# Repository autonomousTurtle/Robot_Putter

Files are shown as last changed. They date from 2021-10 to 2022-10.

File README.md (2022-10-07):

# Robot_Putter
### [May We Help](https://maywehelp.org/) Putt-Putt Robot



## Controls
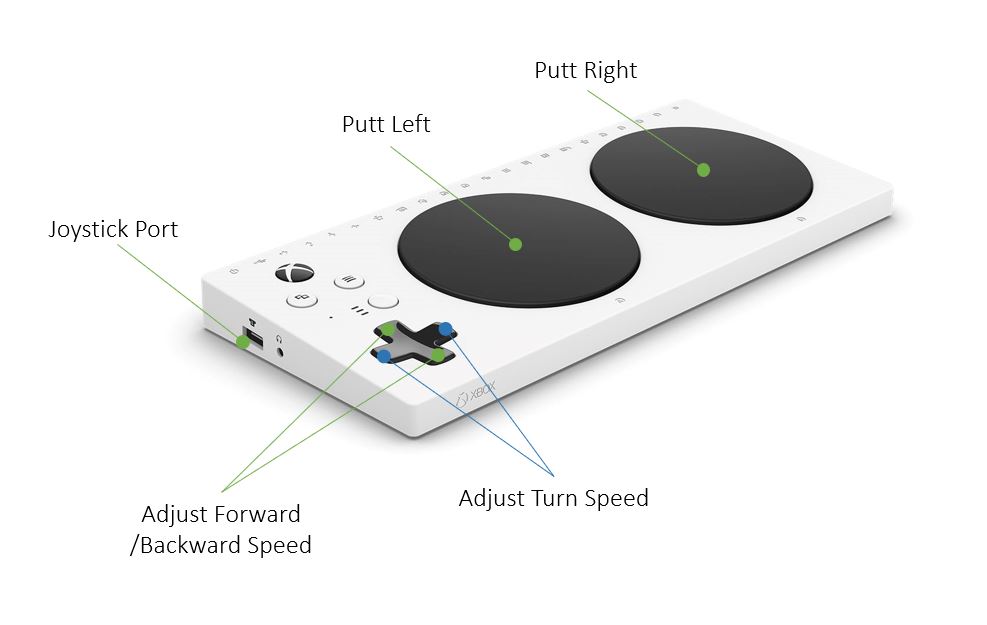
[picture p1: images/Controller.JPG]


## Table Of Contents
1. [BOM](https://github.com/autonomousTurtle/Robot_Putter/blob/main/README.md#bom)
2. [Assembly](https://github.com/autonomousTurtle/Robot_Putter/blob/main/README.md#assembly)
3. [Wiring](https://github.com/autonomousTurtle/Robot_Putter/blob/main/README.md#wiring-images)
4. [Software](https://github.com/autonomousTurtle/Robot_Putter/tree/main/software)

## BOM

### A. Electrical
| Description | Quantity | Ordering Information | Comments |  
| --- | :---: | --- | --- |
|Adafruit Servo Driver Breakout<br>PCA9685|1|[Adafruit](https://www.adafruit.com/product/815)|Adafruit: [Drawings and Tutorials](https://learn.adafruit.com/16-channel-pwm-servo-driver/downloads)|
|Raspberry Pi 4<br>Model B 4GB|1|[CanaKit](https://www.canakit.com/raspberry-pi-4-extreme-kit.html)<br>[Adafruit # 4292](https://www.adafruit.com/product/4292)|CanaKit includes all components necessary to use the pi.<br>Minimum 32GB SD Card|
|Arduino UNO<br>Rev3 ATmega328P|1|[Arduino #A000066](https://store-usa.arduino.cc/products/arduino-uno-rev3)<br>[Sparkfun # DEV-11021](https://www.sparkfun.com/products/11021)|[Elegoo](https://www.elegoo.com/products/elegoo-uno-r3-board) and other brands work fine as well|
|Arduino Shield<br>Through-hole protoboard|1|[Amazon Gikfun](https://www.amazon.com/Gikfun-Prototype-Shield-Arduino-Ek1038x3/dp/B00Q9YB7PI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)|Shields with a 5V and GND rail are the easiest to work with IMO
|Dual Motor Driver<br>L298N|1|[Amazon](https://www.amazon.com/Controller-H-Bridge-Stepper-Control-Mega2560/dp/B07WS89781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)<br>[BC Robotics]https://bc-robotics.com/shop/l298n-motor-driver-board/)|Inludes headers. Drives two DC brushed motors, 1A constant, 3A peak
|12V Battery Pack<br>Dewalt DCB127|[Amazon Dewalt](https://www.amazon.com/DEWALT-DCB127-12V-Lithium-Battery-Pack/dp/B00KYQ1UVS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)<br>[Amazon TenHutt](https://www.amazon.com/dp/B07ZQ9W9RP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)|For use with [12V Dewalt  Charger](https://www.amazon.com/dp/B08FX153FN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)
|Battery Charger<br>Dewalt Charger 12V|1|[Amazon](https://www.amazon.com/dp/B08FX153FN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)
|12V - 6V DC Converter<br>|1|[Amazon](https://www.amazon.com/SMAKN%C2%AE-DC-DC-Converter-Supply-Waterproof/dp/B014ZQ6TFY)|There are many options, most will work. Does not need to be waterproof. Also want to explore this [Digikey R12P06S](https://www.digikey.com/en/products/detail/recom-power/R12P06S/7603362)
|UBEC<br>5V @ 3A DC/DC Buck Converter|1|[Adafruit #1385](https://www.adafruit.com/product/1385)<br>[Amazon](https://www.amazon.com/DEVMO-3amp-6-0-25-2v-Adjustable-Products/dp/B0971H54FQ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)|Used to power the Rasbperry Pi from the 12V battery - must have 5V output, 3A recommended
|Wago Connectors<br>|1|[Digikey 2946-887-952-ND](https://www.digikey.com/en/products/detail/wago-corporation/887-952/15553727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)<br>[Amazon](https://www.amazon.com/Lukche-LEVER-NUTS-Splicing-Connector-Assortment/dp/B095F2Z3DD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)|Other connectors will work (XT60, JST, EC5), Wago simply make it easy to prototype. 

### B. Electro-Mechanical 
| Description | Quantity | Ordering Information | Comments |  
| --- | :---: | --- | --- |
|Putter Servo Motor<br>30KG 270 Degree DS3230|1|[Amazon](https://www.amazon.com/DS3230-30KG-Degree-Digital-Servo/dp/B07VN6F179)<br> [Amazon LJWRC](https://www.amazon.com/LJWRC-DS3230MG-Waterproof-Digital-Degree/dp/B088KJGM4C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)|6.8 V, Full metal gear, waterproof, includes 25T metal servo hub
|Tank Tread Base<br>SZDoit T300|1|[Amazon SZDoit](https://www.amazon.com/dp/B08HRTZNHW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)|Includes qty 2 9V DC motors with encoders
|12V High Torque Motors<br>Geartesian 550RPM|2|[Amazon](https://www.amazon.com/Greartisan-Electric-Reduction-Centric-Diameter/dp/B072R5G5GR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)|
|Adaptive Controller<br>XBox|1|[Best Buy](https://www.bestbuy.com/site/microsoft-xbox-adaptive-controller-white/6455394.p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)|[Any switch with a 3.5mm jack](https://www.ablenetinc.com/switches/all-switches/) can be used with this controller. 
|Warfighter Engaged<br>Joystick FPS|1|[Warfighter](https://warfighterengaged.org/shop/joystix-l-aenef)

### C. Mechanical

| Description | Quantity | Ordering Information | Comments |  
| --- | :---: | --- | --- |
|Printer Filament<br>PLA|1|[MatterHackers M-EED-KTKU](https://www.matterhackers.com/store/l/175mm-pla-filament-white-1-kg/sk/MEEDKTKU)| Color does not matter. Diameter for most filament printers should be 1.75mm |
|Ball Bearing<br>Shielded|1|[Mcmaster ]([https://www.matterhackers.com/store/l/175mm-pla-filament-white-1-kg/sk/MEEDKTKU](https://www.mcmaster.com/5972K293/))| For 30mm shaft diameter |

### D. 3D Prints
All of the custom parts are 3D Printed on a filamnet printer with PLA. 

| Description | Quantity | Ordering Information | Comments |  
| --- | :---: | --- | --- |
|Putter Servo Mount|1|[Putter_Servo_holder_A.STL](https://github.com/autonomousTurtle/Robot_Putter/blob/main/3D%20Prints/Putter_Servo_holder_A.STL) <br> [Putter_Servo_holder_B.STL](https://github.com/autonomousTurtle/Robot_Putter/blob/main/3D%20Prints/Putter_Servo_holder_B.STL) | Holds the 30kg-cm servo, left and right parts |
|Ball Bearing Inner Housing|1|[BallBearingAttachToRobot_Big_1.STL](https://github.com/autonomousTurtle/Robot_Putter/blob/main/3D%20Prints/BallBearingAttachToRobot_Big_1.STL)| Mounts to Cover Front part |
|Ball Bearing Outer Housing|1|[BallBearingAttachToRobot_little_1.STL](https://github.com/autonomousTurtle/Robot_Putter/blob/main/3D%20Prints/BallBearingAttachToRobot_little_1.STL)| Holds ball bearing in place wtih the inner housing |
|Servo Horn Attachment|1|[GolfClubAttach_rev2_bottom_1.STL](https://github.com/autonomousTurtle/Robot_Putter/blob/main/3D%20Prints/GolfClubAttach_rev2_bottom_1.STL)| Attaches the servo horn and fits inside of the ball bearing |
|Putter Shaft Holder|1|[GolfClubAttach_rev2_top_1.STL](https://github.com/autonomousTurtle/Robot_Putter/blob/main/3D%20Prints/GolfClubAttach_rev2_top_1.STL)| Attaaches to the putter shaft on one end and to the Servo Horn Attachment on the other end |
|Putter Head|1|[PutterHead.STL](https://github.com/autonomousTurtle/Robot_Putter/blob/main/3D%20Prints/PutterHead.STL)| Feel free to use whatever putter head you want, but 3D printing makes the robot lighter |
|Motor Driver Breakout Board Mount|1|[Motor_Driver_Board_Holder_rev1.STL](https://github.com/autonomousTurtle/Robot_Putter/blob/main/3D%20Prints/Motor_Driver_Board_Holder_rev1.STL)| Mounts the L298N breakout board to the bottom plate of the robot base |
|Arduino Uno Mount|1|[Arduino_mount.STL](https://github.com/autonomousTurtle/Robot_Putter/blob/main/3D%20Prints/Arduino_mount.STL)| Used for attaching the Uno to the top of the raspberry pi cana kit case |
|Servo Driver Board Mount|1|[Servo_Driver_Mount.STL](https://github.com/autonomousTurtle/Robot_Putter/blob/main/3D%20Prints/Servo_Driver_Mount.STL)| Attach the servo driver to the base plate |
|Cover Front|1|[cover_front_0.STL](https://github.com/autonomousTurtle/Robot_Putter/blob/main/3D%20Prints/cover_front_0.STL)| Covers the front of the robot internals |
|Cover Rear|1|[cover_back_0.STL](https://github.com/autonomousTurtle/Robot_Putter/blob/main/3D%20Prints/cover_back_0.STL)| Covers the rear of the robot internals |
|Cover Top|1|[cover_top_cover_0.STL](https://github.com/autonomousTurtle/Robot_Putter/blob/main/3D%20Prints/cover_top_cover_0.STL) | I used clear Lexan for this, but you can also 3D print it |

### Assembly

#### Parts Laid Out
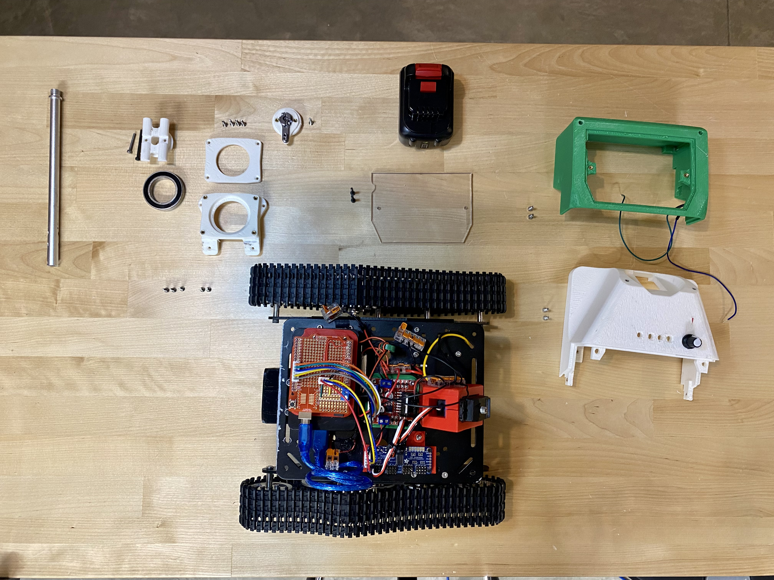
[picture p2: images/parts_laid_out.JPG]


#### Bottom Side
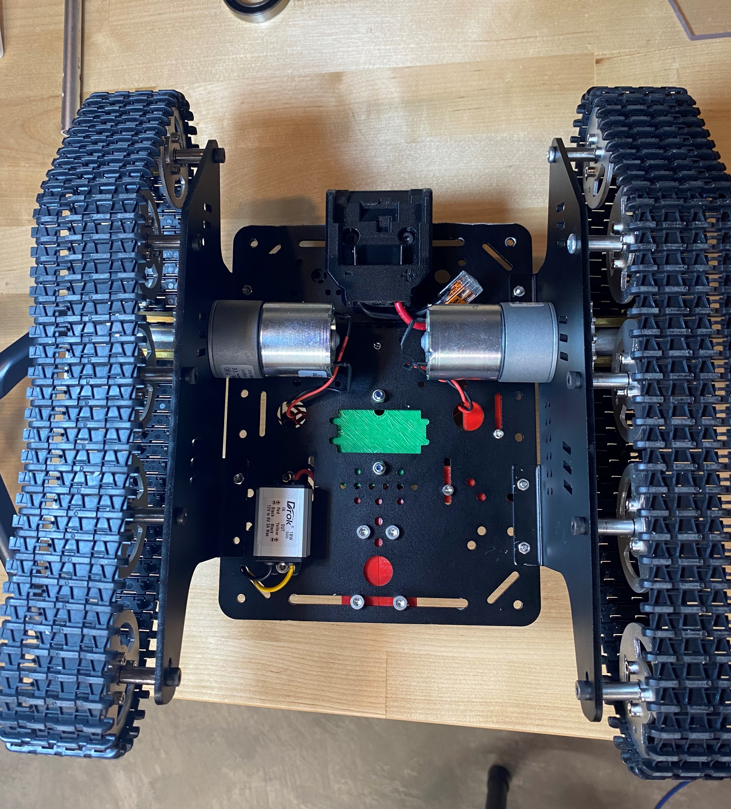
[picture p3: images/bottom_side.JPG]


#### Top Without Cover
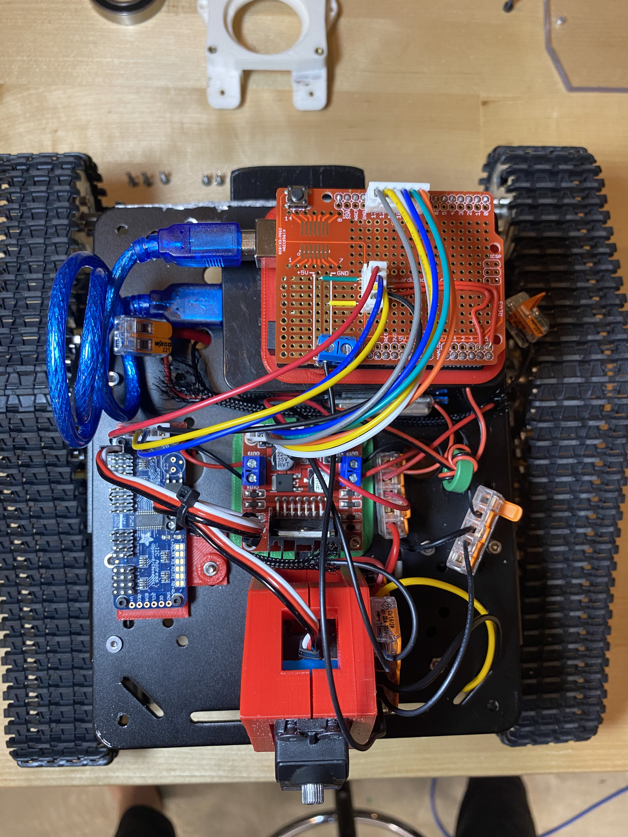
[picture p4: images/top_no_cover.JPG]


### Wiring Images
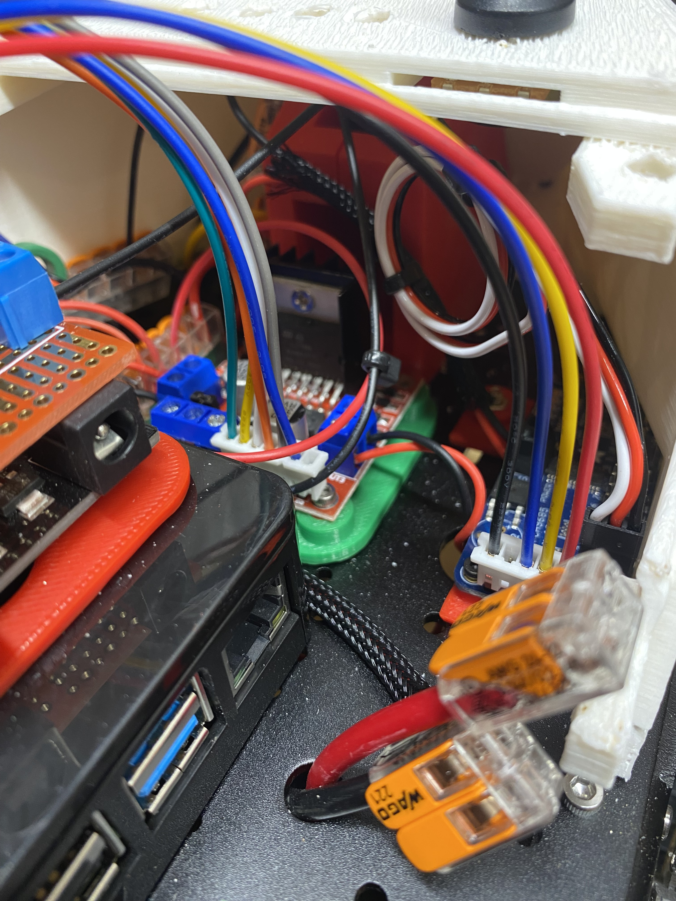
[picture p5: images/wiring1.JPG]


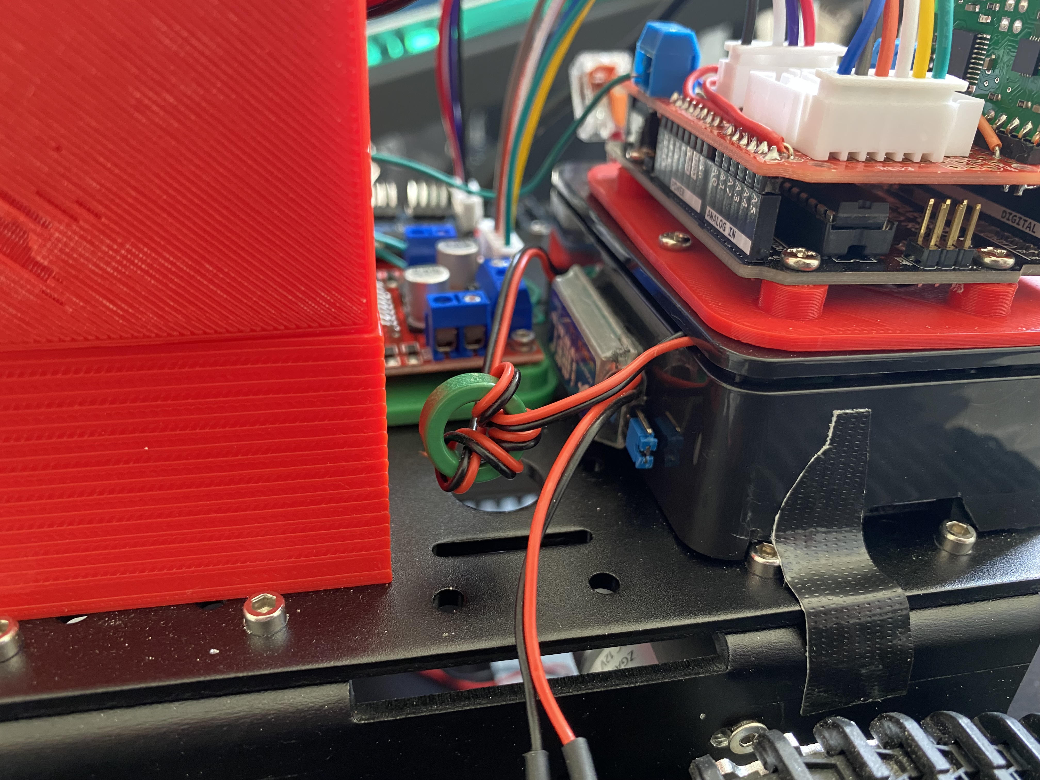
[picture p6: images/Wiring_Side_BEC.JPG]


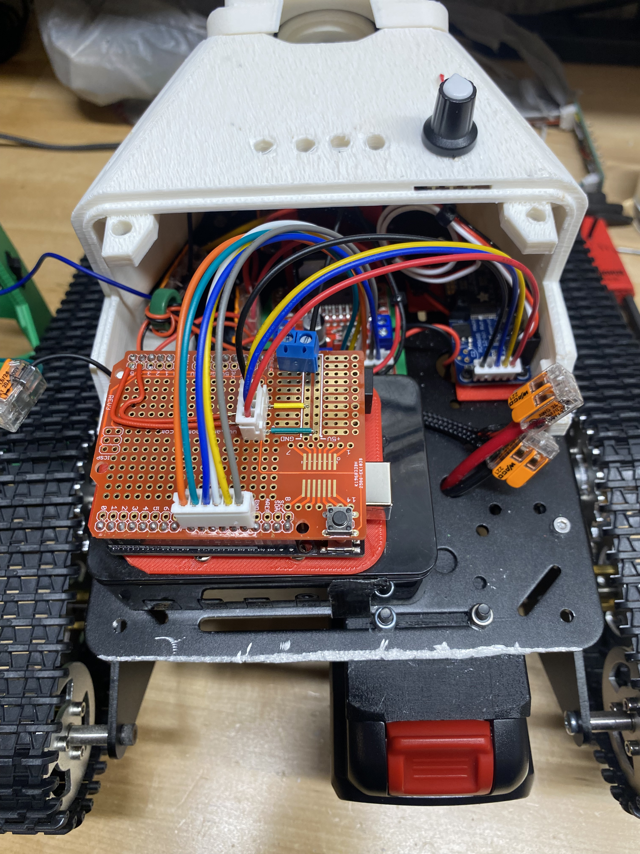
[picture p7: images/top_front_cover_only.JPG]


### Software Architecture:

* Arduino:  software/drive_and_putt/drive_and_putt.ino
* Raspberry Pi: software/deployed/drive_robot.py

See the [software readme for more details](https://github.com/autonomousTurtle/Robot_Putter/tree/main/software)

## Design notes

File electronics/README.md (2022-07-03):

# ROBOT PUTTER ELECTRONICS

### Detailed Wiring
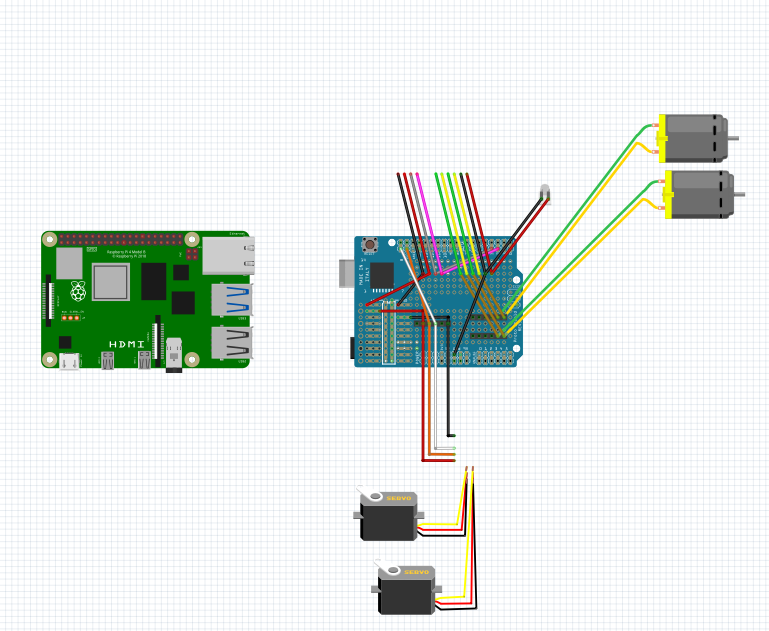
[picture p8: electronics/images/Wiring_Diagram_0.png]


### 1. Electrical Components
| Description | Quantity | Ordering Information | Comments |  
| --- | :---: | --- | --- |
|Adafruit Servo Driver Breakout<br>PCA9685|1|[Adafruit](https://www.adafruit.com/product/815)|Adafruit: [Drawings and Tutorials](https://learn.adafruit.com/16-channel-pwm-servo-driver/downloads)|
|Raspberry Pi 4<br>Model B 4GB|1|[CanaKit](https://www.canakit.com/raspberry-pi-4-extreme-kit.html)<br>[Adafruit # 4292](https://www.adafruit.com/product/4292)|CanaKit includes all components necessary to use the pi.<br>Minimum 32GB SD Card|
|Arduino UNO<br>Rev3 ATmega328P|1|[Arduino #A000066](https://store-usa.arduino.cc/products/arduino-uno-rev3)<br>[Sparkfun # DEV-11021](https://www.sparkfun.com/products/11021)|[Elegoo](https://www.elegoo.com/products/elegoo-uno-r3-board) and other brands work fine as well|
|Arduino Shield<br>Through-hole protoboard|1|[Amazon Gikfun](https://www.amazon.com/Gikfun-Prototype-Shield-Arduino-Ek1038x3/dp/B00Q9YB7PI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)|Shields with a 5V and GND rail are the easiest to work with IMO
|Dual Motor Driver<br>Pololu Qik 2s9v1|1|[Pololu #1110](https://www.pololu.com/product/1110)<br>[DigiKey # 2183-1110-ND](https://www.digikey.com/en/products/detail/pololu-corporation/1110/10450402)|Inludes headers. Drives two DC brushed motors, 1A constant, 3A peak
|12V Battery Pack<br>Tenergy 2000mAh NiMH|2|[Amazon](https://www.amazon.com/Tenergy-Capacity-Rechargeable-Replacement-Equipments/dp/B077Y9HNTF?th=1)<br>[Tenergy Power #11606](https://power.tenergy.com/tenergy-nimh-12v-2000mah-battery-pack-w-bare-leads/)|Requires [T-Plug headers](https://www.progressiverc.com/products/t-plug-connectors) <br>For use with [6V-12V Tenergy Smart Charger](https://power.tenergy.com/tenergy-smart-universal-charger-for-nimh-nicd-battery-packs-6v-12v-ul/)
|Battery Charger<br>Tenergy NiMH Charger 6-12V|1|[Tenergy Power #01025](https://power.tenergy.com/tenergy-smart-universal-charger-for-nimh-nicd-battery-packs-6v-12v-ul/)|Can also use [Tenergy NiHM 7.2-12V Charger](https://power.tenergy.com/tenergy-smart-universal-charger-for-nimh-nicd-battery-packs-7-2v-12v-ul/)
|AI 3D Camera<br>Luxonis OAK-D|1|[Luxonis OAK-D](https://shop.luxonis.com/products/oak-d)<br>[DigiKey #SEN-17770](https://www.digikey.in/en/products/detail/sparkfun-electronics/SEN-17770/13901888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)|Requires high throughput USBC cable, inlcuded with camera
|12V - 6V DC Converter<br>|1|[Amazon](https://www.amazon.com/SMAKN%C2%AE-DC-DC-Converter-Supply-Waterproof/dp/B014ZQ6TFY)|There are many options, most will work. Does not need to be waterproof. Also want to explore this [Digikey R12P06S](https://www.digikey.com/en/products/detail/recom-power/R12P06S/7603362)
|UBEC<br>5V @ 3A DC/DC Buck Converter|1|[Adafruit #1385](https://www.adafruit.com/product/1385)<br>[Amazon](https://www.amazon.com/DEVMO-3amp-6-0-25-2v-Adjustable-Products/dp/B0971H54FQ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)|Used to power the Rasbperry Pi from the 12V battery - must have 5V output, 3A recommended
|T-Plug Connectors<br>|1|[ProgressiveRC #AC-TC](https://www.progressiverc.com/products/t-plug-connectors)<br>[Amazon](https://www.amazon.com/Hobbypark-T-Plug-Connectors-Battery-Electric/dp/B01C8NWJ78)|Other battery connectors will work (XT60, JST, EC5) just make sure it is secure. 
|Wire Heat Shirnk Wrap<br>|1|[Amazon](https://www.amazon.com/650pcs-Shrink-Tubing-innhom-Approved/dp/B07WWWPR2X)<br>|A kit with a variety of sizes helps to have what is needed for different wire gauges

### 2. Electro-Mechanical 
| Description | Quantity | Ordering Information | Comments |  
| --- | :---: | --- | --- |
|Putter Servo Motor<br>30KG 270 Degree DS3230|1|[Amazon](https://www.amazon.com/DS3230-30KG-Degree-Digital-Servo/dp/B07VN6F179)<br> [Amazon LJWRC](https://www.amazon.com/LJWRC-DS3230MG-Waterproof-Digital-Degree/dp/B088KJGM4C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)|6.8 V, Full metal gear, waterproof, includes 25T metal servo hub
|Camera Servo Motor<br>20KG 270 Degree DS3218MG|1|[Amazon ANNIMOS](https://www.amazon.com/ANNIMOS-Digital-Waterproof-DS3218MG-Control/dp/B076CNKQX4)<br>[Amazon ZOSKAY](https://www.amazon.com/ZOSKAY-DS3218-Digital-Waterproof-Control/dp/B01MU7TQV8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)|6.8 V, Full metal gear, waterproof, includes 25T metal servo hub
|Tank Tread Base<br>SZDoit T300|1|[Amazon SZDoit](https://www.amazon.com/dp/B08HRTZNHW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)|Includes qty 2 9V DC motors with encoders
|Adaptive Controller<br>Nintendo HORI Flex|1|[HORI #NSW-280U](https://stores.horiusa.com/flex-controller-for-nintendo-switch/?showHidden=true)|[Any switch with a 3.5mm jack](https://www.ablenetinc.com/switches/all-switches/) can be used with this controller.

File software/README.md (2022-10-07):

# SOFTWARE 

## Overview: 

This robot uses [subsumption control architecure](https://en.wikipedia.org/wiki/Subsumption_architecture) to manage both a Raspberry Pi and an Arduino microcontroller. The Arduino is responsible for the low level management: motor control, servo control, LED control. The Raspberry Pi is responsible for the higer level control: talking to the XBox controller, ensure the robot si driving straight, when to move the putter vs when to move the motors, speed ramping and more. 

In this architecture, the raspberry pi is sending strings of commands to the Arduino. The Arduino looks at the commands and executes the necessary code to make the desired actions happen. When there are no actions called for from the Pi, they communicate back and forth at 2hz with a heartbeat. If the Pi or Arduino fail to send or recieve a heartbeat signal, they will stop all motion and shut down their processes. This is an important safety mechanism to prevent run-away robots! 

## Code: 
**Python Script run on Raspberry Pi:** [drive_robot.py](https://github.com/autonomousTurtle/Robot_Putter/blob/main/software/deployed/drive_robot.py)

_this code will start automatically with an auto-run script, but to run manually through ssh, navigate to the root folder and type:_

`$ python3 drive_robot.py`

**Arduino Script:** [drive_and_putt.ino](https://github.com/autonomousTurtle/Robot_Putter/blob/main/software/drive_and_putt/drive_and_putt.ino)

## Rapsberry Pi Connections:

### LAN
Raspberry Pi eth0 IP: 192.168.0.1 (ethernet port on the Pi)
Raspberry Pi LAN IP: 192.168.7.21

### WAN and SSH
username: pi@192.168.7.129
password: raspberry

## Configuring the Raspberry Pi:

### Serial
You need to configure serial on the Pi to be able to talk to Aruduino board. You do this by giving the user dialout permissions:

`usermod -a -G dialout $USER`

### Auto Run Python Script 
We need to automatically run the drive_robot.py script on boot of the rpi. [Link here is hlepful to get it set up](https://www.codementor.io/@ufukafak/how-to-run-a-python-script-in-linux-with-systemd-1nh2x3hi0e_)

## Pi Libraries:

### Read Controller Inputs
[PiBorg Gamepad Library](https://www.piborg.org/blog/gamepad-library): [Github Link](https://github.com/piborg/Gamepad)

This library is great becuases it has built in asynchronous updates in a background thread. 

```
import Gamepad
gamepad = Gamepad.PS4()

# Start the background updating
gamepad.startBackgroundUpdates()

# Your code here :)

# Stop the background thread
gamepad.disconnect()
```

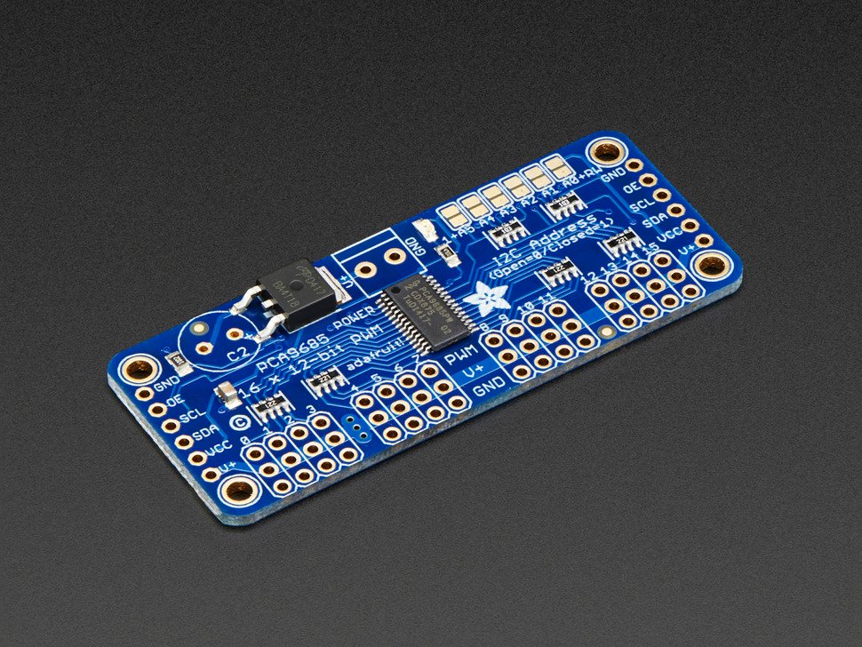
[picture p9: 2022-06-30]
electronics/images/adafruit_servo_breakout.jpg

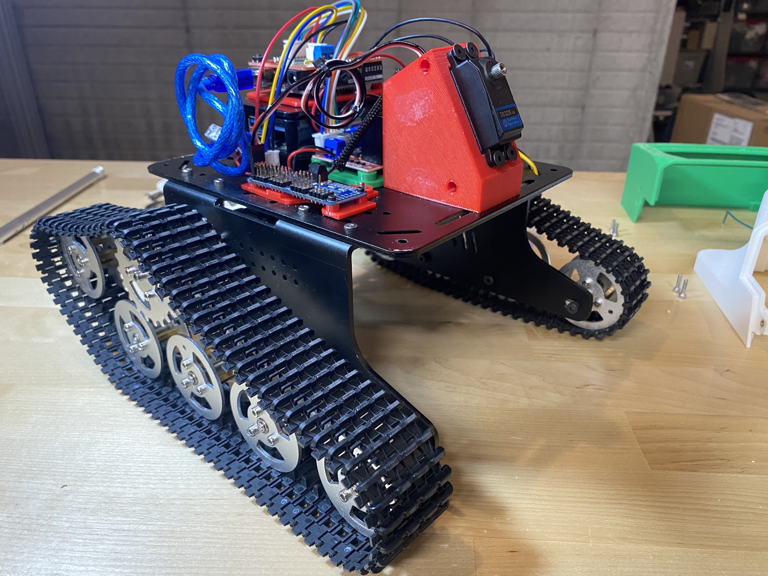
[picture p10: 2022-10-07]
images/iso_no_cover.JPG

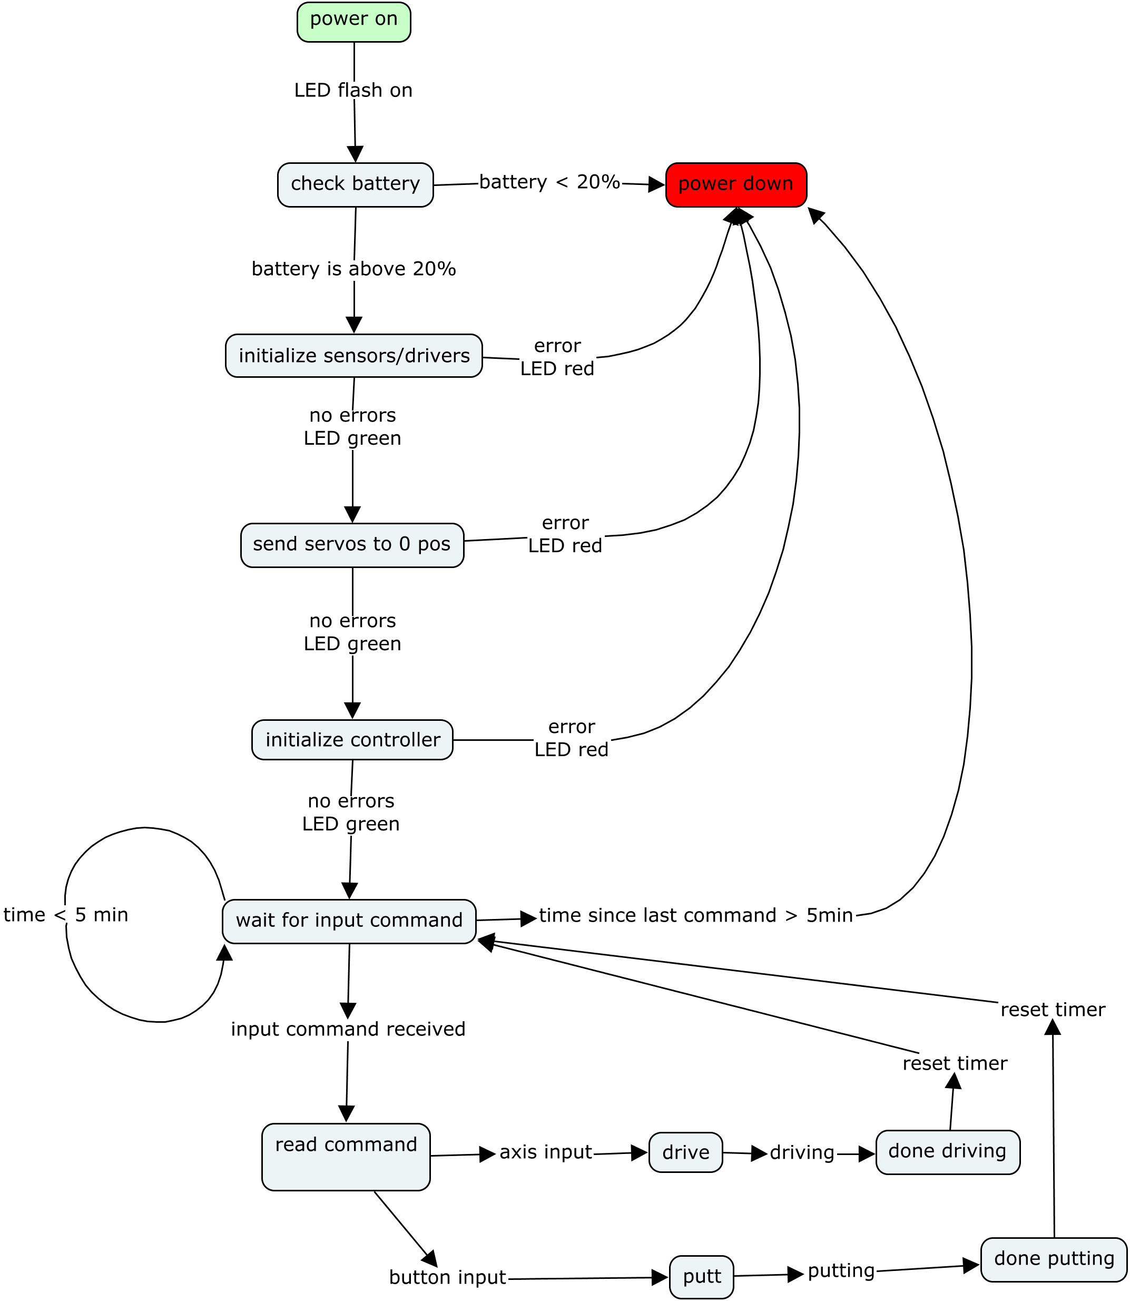
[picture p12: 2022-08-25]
software/Putt Robot State Machine.png

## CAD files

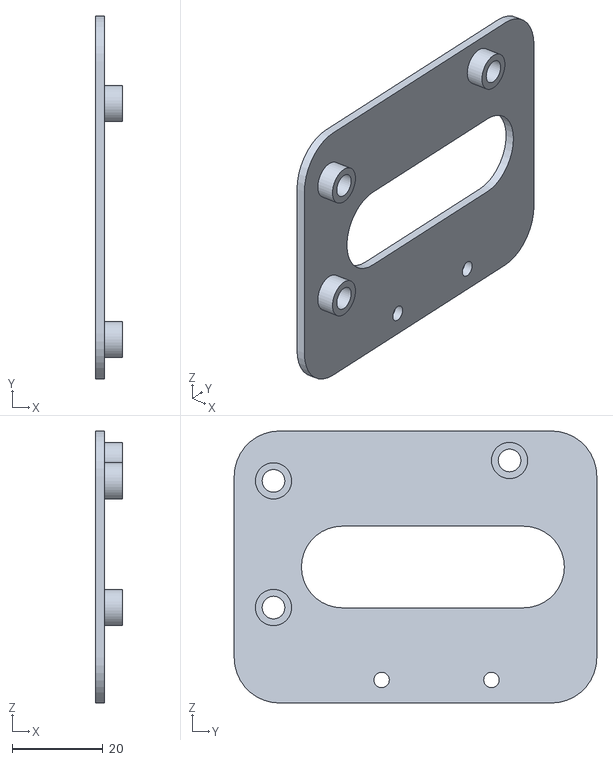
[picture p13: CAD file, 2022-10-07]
3D Prints/Arduino_mount.STL
6.00 x 80.0 x 60.0

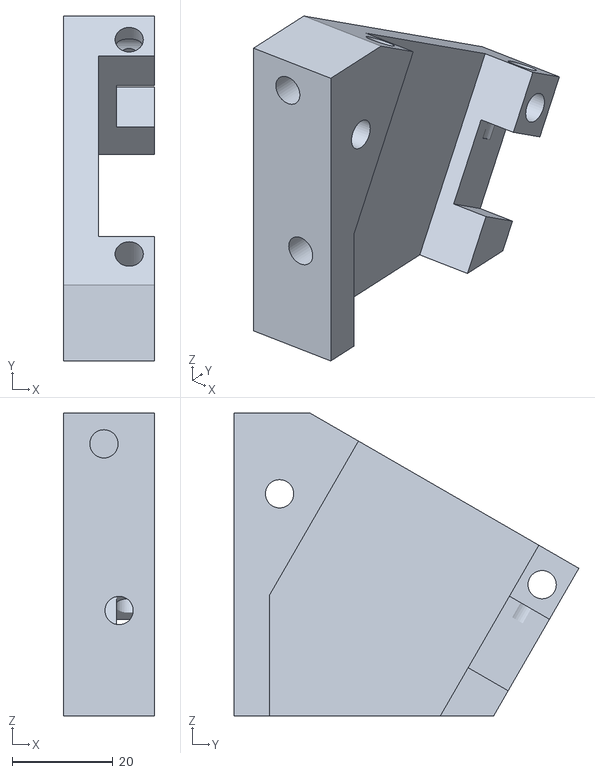
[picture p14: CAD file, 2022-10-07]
3D Prints/Putter_Servo_holder_A.STL
18.0 x 68.3 x 60.0

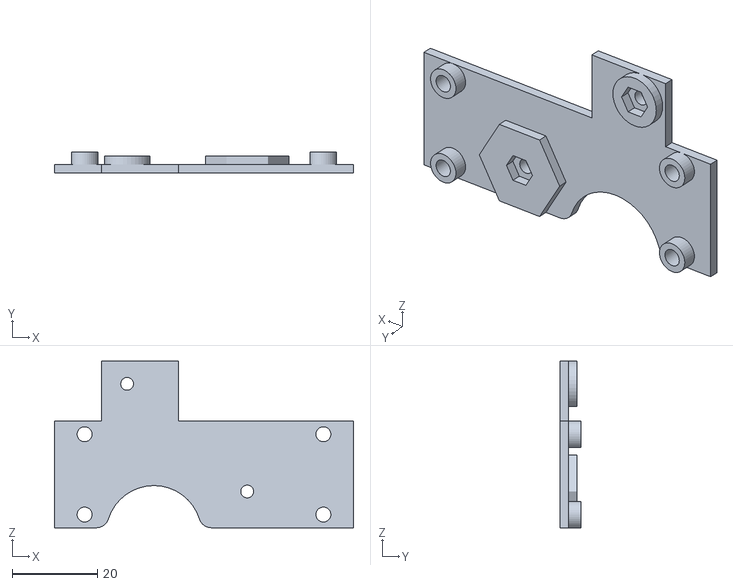
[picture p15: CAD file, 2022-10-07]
3D Prints/Servo_Driver_Mount.STL
70.0 x 5.00 x 39.0

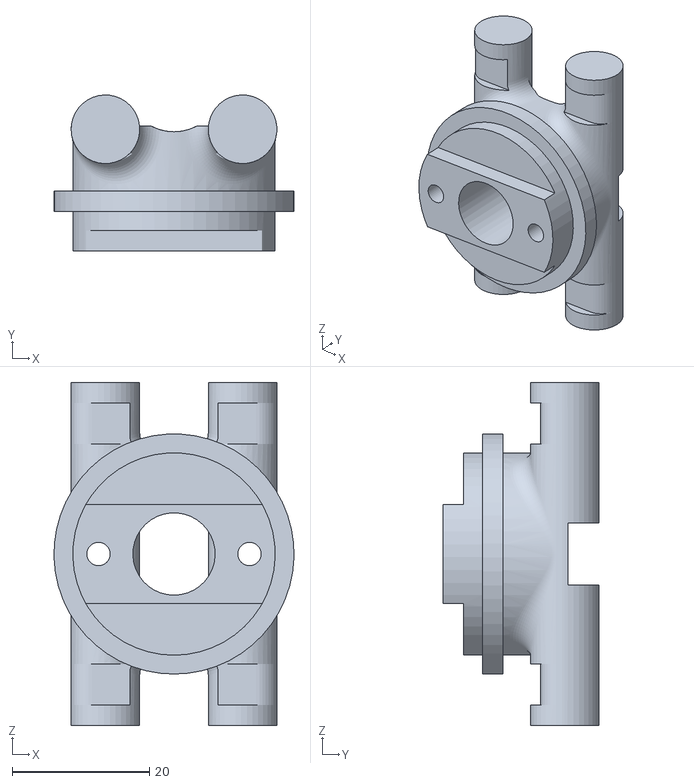
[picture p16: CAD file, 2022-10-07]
3D Prints/GolfClubAttach_rev2_top_1.STL
35.0 x 22.7 x 50.0

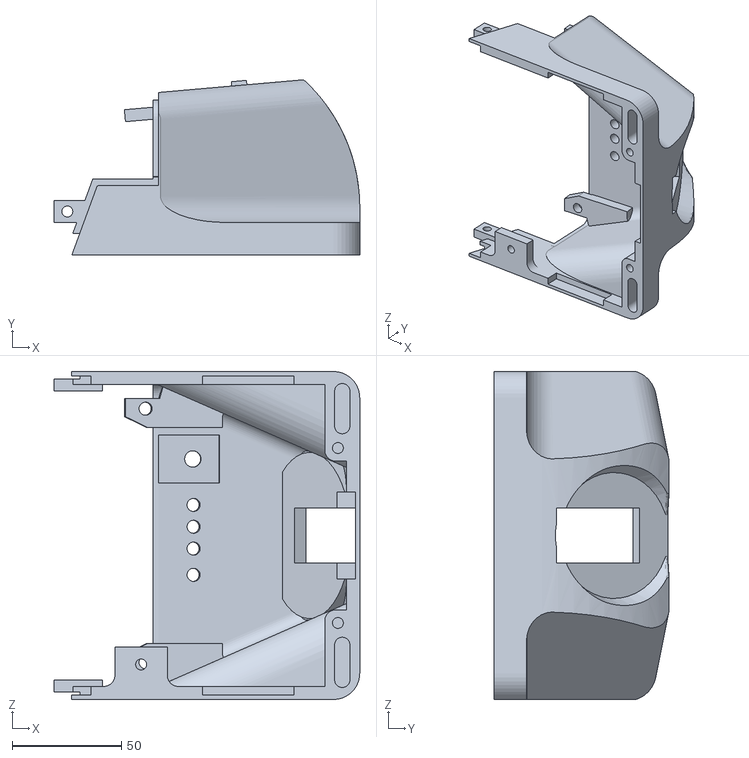
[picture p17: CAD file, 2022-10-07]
3D Prints/cover_front_0.STL
139.7 x 80.3 x 150.0

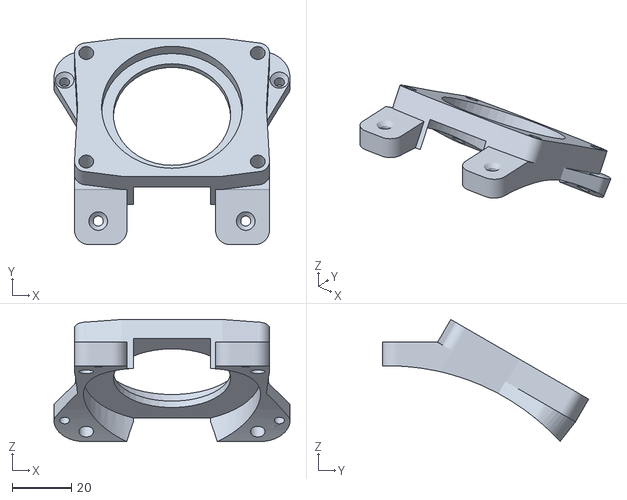
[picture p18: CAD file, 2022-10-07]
3D Prints/BallBearingAttachToRobot_Big_1.STL
80.0 x 70.0 x 41.4

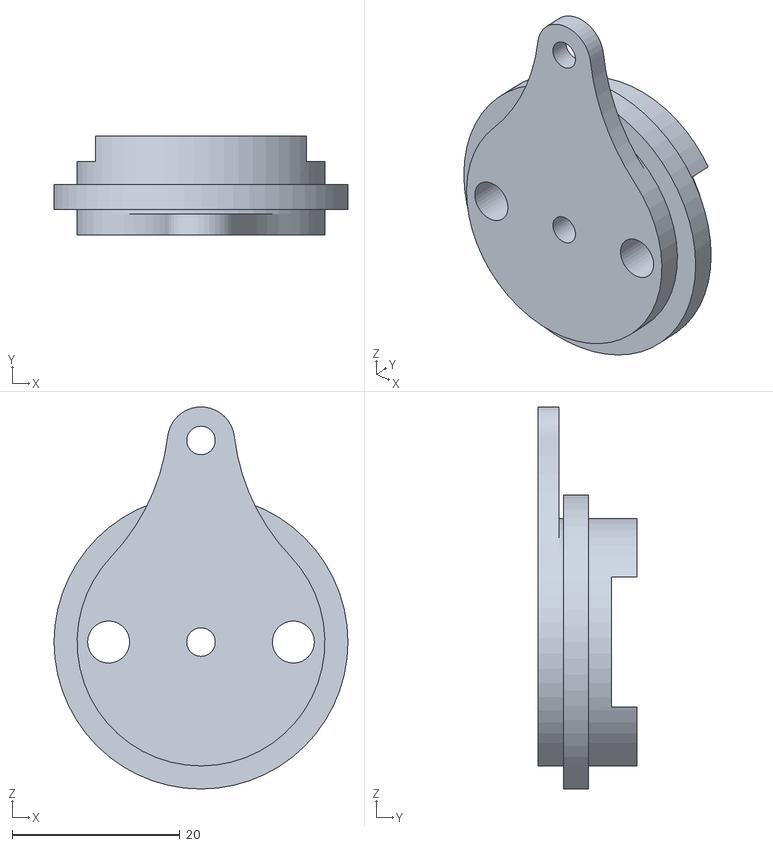
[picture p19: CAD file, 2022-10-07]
3D Prints/GolfClubAttach_rev2_bottom_1.STL
35.0 x 11.8 x 45.5

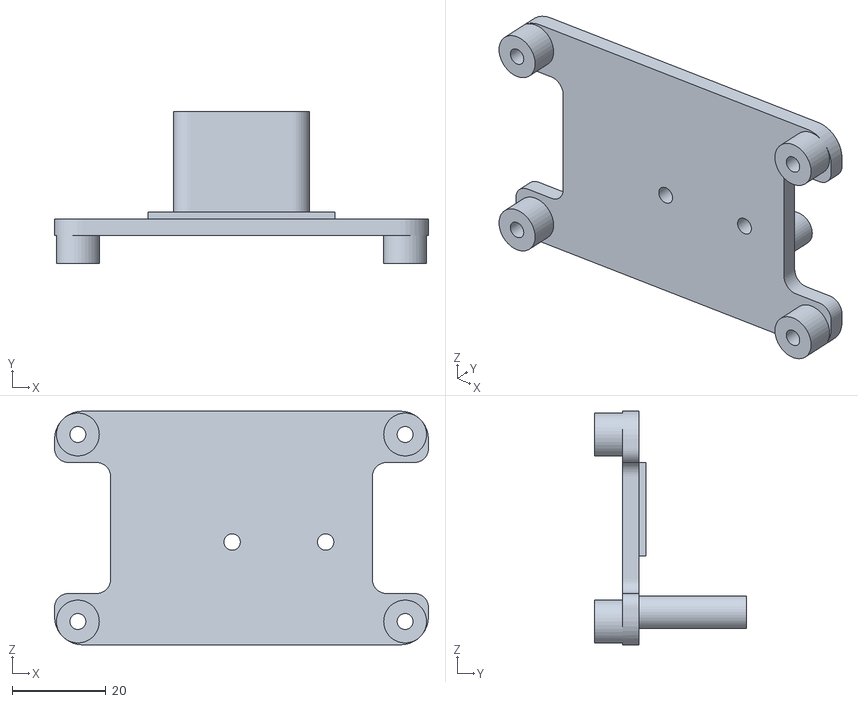
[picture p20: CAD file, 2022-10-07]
3D Prints/Motor_Driver_Board_Holder_rev1.STL
80.0 x 32.5 x 50.0

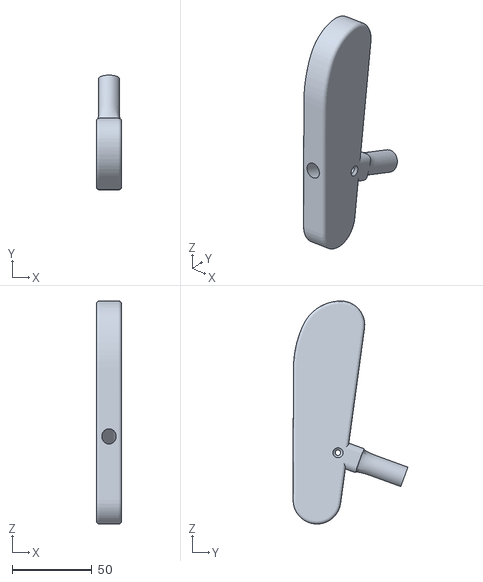
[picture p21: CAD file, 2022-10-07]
3D Prints/PutterHead.STL
16.0 x 72.1 x 140.0

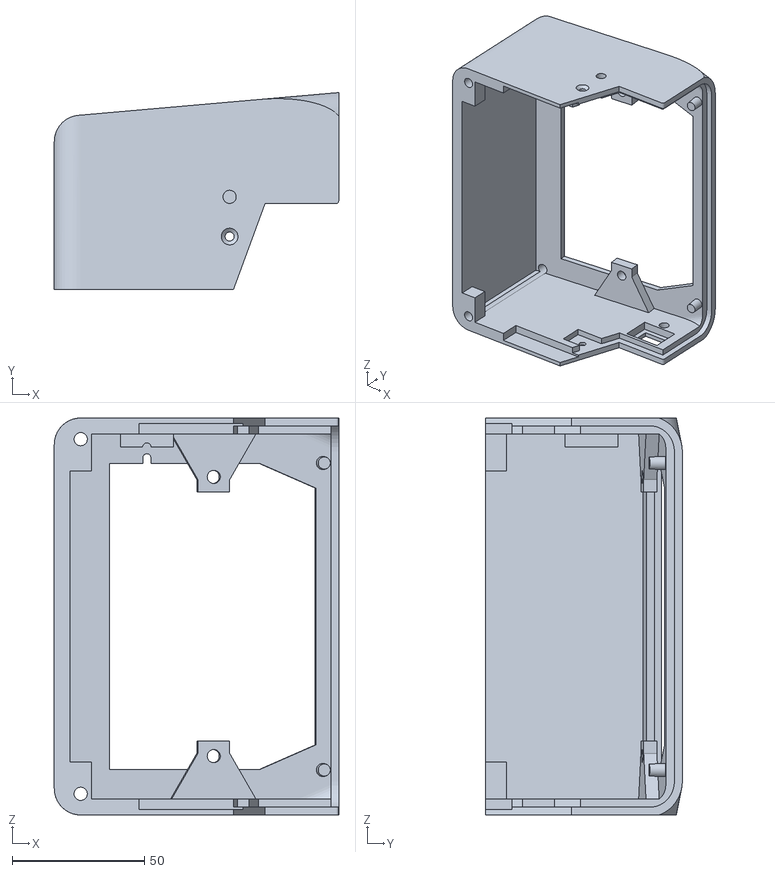
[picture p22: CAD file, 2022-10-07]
3D Prints/cover_back_0.STL
107.5 x 74.4 x 150.0

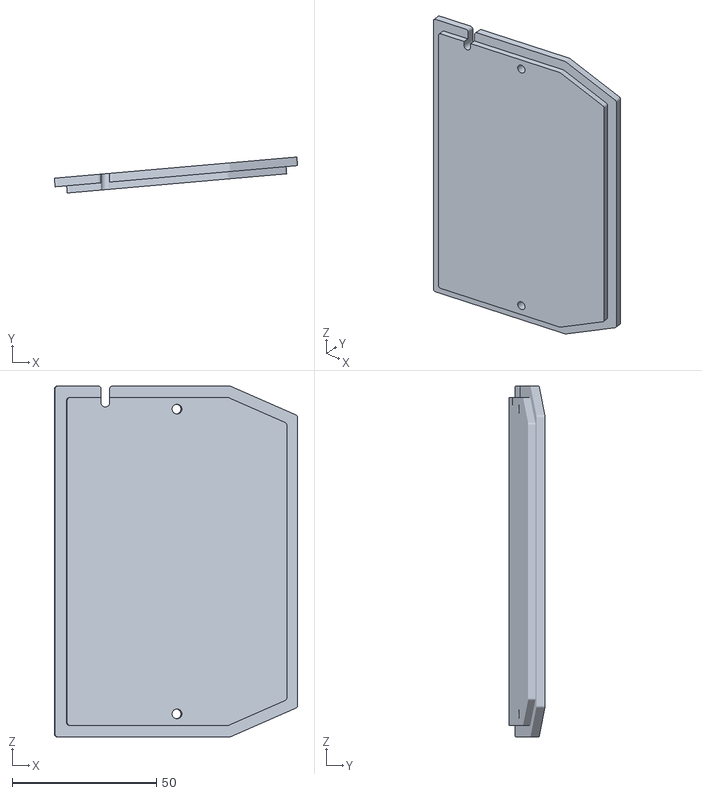
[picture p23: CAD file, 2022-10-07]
3D Prints/cover_top_cover_0.STL
84.2 x 12.5 x 121.5

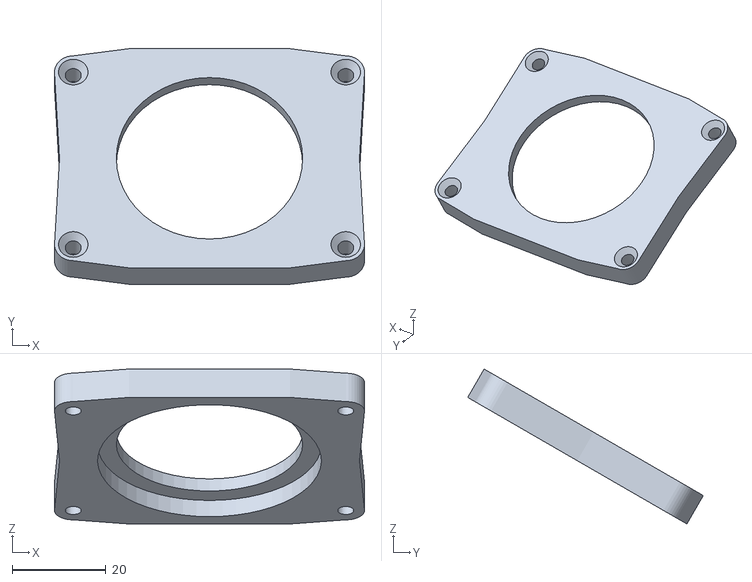
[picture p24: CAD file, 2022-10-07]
3D Prints/BallBearingAttachToRobot_little_1.STL
66.1 x 50.3 x 33.1

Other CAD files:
3D Prints/Putter_Servo_holder_B.STL

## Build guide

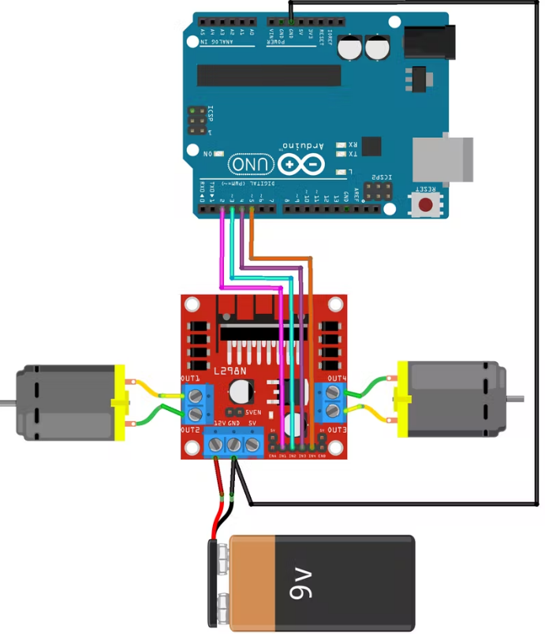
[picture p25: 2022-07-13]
software/images/L298N Wiring.png

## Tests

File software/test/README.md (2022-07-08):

# Test Software

For all tests, run the python script on the Raspberry Pi and .ino script on the Arduino
## Communication Test

### Python Script: 
Takes in keyboard w,a,s,d inputs and sends fake commands to the arduino. It also sends a heartbeat meassage twice a second. 

### Arduino Script: 

## Motor Test
### Python Script: 

### Arduino Script:

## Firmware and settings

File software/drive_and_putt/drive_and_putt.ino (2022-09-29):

/***************************************************

  Online Libraries:
  Timer.h - JChristhensen's Timer Library https://github.com/JChristensen/Timer
  Event.h - Arcturial arduino event https://github.com/arcturial/arduino-event
  Link to the Adafruit PWM Servo Driver  http://www.adafruit.com/products/815

  Link to Raspberry Pi to Arduino Serial Comm:
  https://www.aranacorp.com/en/serial-communication-between-raspberry-pi-and-arduino/


 ****************************************************/

#include <Adafruit_PWMServoDriver.h>
#include <Wire.h>
#include <Timer.h>
#include <Event.h>


// ---------- L298N Motor Driver ---------
#define enA 9
#define in1 12
#define in2 11
#define in3 8
#define in4 13
#define enB 10


// ---------- LED Pins ---------
#define LED1 3  // status LED, green is online and HB is good
#define LED2 2
#define LED3 4
#define LED4 5


// ---------- SERVO DRIVER -----------
Adafruit_PWMServoDriver pwm = Adafruit_PWMServoDriver(); // called this way, it uses the default address 0x40

#define SERVOMIN  150 // This is the 'minimum' pulse length count (out of 4096)
#define SERVOMAX  600 // This is the 'maximum' pulse length count (out of 4096)
#define SERVO_FREQ 50 // Analog servos run at ~50 Hz updates

// Servo home positions (in microsecond length)
const int servo0_home = 300;
const int servo1_home = 280;


// ---------- RASBPERRY PI COMMS ----------
int timerEvent;
int hti; //heartbeat timeout interfal
boolean hbb; //heartbeat fail indication
Timer timer;
const byte inDataLen = 28;
char inData[inDataLen]; // buffer input commands
char messageFromPC[inDataLen] = {0};
double HBBtime = 0;
double LMotorInput;
double RMotorInput;

boolean newData = false; // detect new data into the arduino from the pi

boolean between(int in, int lower, int upper) {
  boolean result = false;
  if ((in <= upper) && (in >= lower)) {
    result = true;
  }
  return result;
}


void clearHBB() {
  hbb = false;
  timerEvent = timer.after(hti, clearHBB);
  // stop all of the motors
  analogWrite(enA, 0); // Send PWM signal to L298N Enable pin
  analogWrite(enB, 0); // Send PWM signal to L298N Enable pin
  digitalWrite(LED1, LOW);
}


void ALLSTOP() {
  analogWrite(enA, 0); // Send PWM signal to L298N Enable pin
  analogWrite(enB, 0); // Send PWM signal to L298N Enable pin
  Serial.write("All Stop\n");
}


void setup() {
  // Start serial communication with the PC
  Serial.begin(115200);
  hti = 1000;
  timerEvent = timer.after(hti, clearHBB);
  
  // ---------- L298N Pin Settings ---------
  pinMode(enA, OUTPUT);
  pinMode(in1, OUTPUT);
  pinMode(in2, OUTPUT);
  pinMode(enB, OUTPUT);
  pinMode(in3, OUTPUT);
  pinMode(in4, OUTPUT);

  pinMode(LED1, OUTPUT);
  pinMode(LED2, OUTPUT);
  pinMode(LED3, OUTPUT);
  pinMode(LED4, OUTPUT);
  

  // Set initial rotation direction
  digitalWrite(in1, LOW);
  digitalWrite(in2, HIGH);

  digitalWrite(LED1, LOW);
  digitalWrite(LED2, LOW);
  digitalWrite(LED3, LOW);
  digitalWrite(LED4, LOW);

  // servo driver
  pwm.begin();
  pwm.setOscillatorFrequency(27000000);
  pwm.setPWMFreq(SERVO_FREQ);  // Analog servos run at ~50 Hz updates


  delay(100); 

  // set servos to 0 position
  pwm.setPWM(0, 0, servo0_home); // putter servo
  pwm.setPWM(1, 0, servo1_home); // camera servo

  Serial.println("ready >");

  delay(500);

}

void loop() {
  char EOL = '>';
  static byte ndx = 0;

  timer.update();

  if (Serial.available() > 0) {
    char inChar = Serial.read();

    if (inChar != EOL) {
      inData
      [ndx] = inChar;
      ndx++;
      if (ndx >= inDataLen) {
        ndx =  inDataLen - 1;
      }
    }
    else if (inChar == EOL) {
      inData[ndx] = '\0'; // terminate the string
      ndx = 0;
      newData = true;
    }
  }

  if (newData == true) {

    // parse the data commas are the seperator

    // split the data into its parts
    char * strtokIndx; //
    strtokIndx = strtok(inData, ","); // get the first part, the string (HBB, DRV, STP..)
    strcpy(messageFromPC, strtokIndx); // copy the string to the messageFromPC char


    if (messageFromPC[0] == 'S') {
      // stop!
      Serial.print("STOP CMD\n");
      ALLSTOP();
      digitalWrite(LED1, LOW); //status LED on 
    }

    // heartbeat - check this first
    if (messageFromPC[0] == 'H') {
      digitalWrite(LED1, HIGH); //status LED on 
      // parse the time data
      strtokIndx = strtok(NULL, ","); // continues where we left off in the message
      //strcpy(HBBtime, strtokIndx);
      //Serial.print(strtokIndx);
      HBBtime = atof(strtokIndx);

      // just put it right back out the serial port
      Serial.print("HBB ");
      Serial.print(HBBtime);
      Serial.println(">");
      hbb = true;
      timer.stop(timerEvent); //candel the last timer
      // set a timer that goes off in 2 seconds
      timerEvent = timer.after(hti, clearHBB);
      
    }

    if (messageFromPC[0] == 'D') {
      hbb = true;
      digitalWrite(LED1, HIGH); //status LED on 
      timer.stop(timerEvent);
      timerEvent = timer.after(hti, clearHBB);
      // parse data

      strtokIndx = strtok(NULL, ","); // continues where we left off in the message
      RMotorInput = atof(strtokIndx);
      strtokIndx = strtok(NULL, ","); // continues where we left off in the message
      LMotorInput = atof(strtokIndx);

      // set motor directions based on incoming commands
      if (RMotorInput > 0) {
        digitalWrite(in1, 0);
        digitalWrite(in2, 1);
      }
      else if (RMotorInput < 0) {
        digitalWrite(in1, 1);
        digitalWrite(in2, 0);
        RMotorInput = -RMotorInput;
      }

      if (LMotorInput > 0) {
        digitalWrite(in3, 0);
        digitalWrite(in4, 1);
      }
      else if (LMotorInput < 0) {
        digitalWrite(in3, 1);
        digitalWrite(in4, 0);
        LMotorInput = -LMotorInput;
      }

      //set motors speeds
      analogWrite(enA, RMotorInput); // Send PWM signal to L298N Enable pin
      analogWrite(enB, LMotorInput); // Send PWM signal to L298N Enable pin
      Serial.print("DRV ");
      Serial.print(RMotorInput);
      Serial.println(">");
    }

    if (messageFromPC[0] == 'P') {
      hbb = true;
      digitalWrite(LED2, HIGH);
      digitalWrite(LED1, HIGH); //status LED on 
      Serial.print("Putting");
      Serial.print(">");

      strtokIndx = strtok(NULL, ","); // continues where we left off in the message
      double motor0input = atof(strtokIndx);
      strtokIndx = strtok(NULL, ","); // continues where we left off in the message
      double motor1input = atof(strtokIndx);
      strtokIndx = strtok(NULL, ","); // continues where we left off in the message
      double motor2input = atof(strtokIndx);
      strtokIndx = strtok(NULL, ","); // continues where we left off in the message
      double gripperInput = atof(strtokIndx);

      Serial.print("ARM:");
      Serial.print(motor0input);
      Serial.print(",");
      Serial.print(motor1input);
      Serial.print(",");
      Serial.print(motor2input);
      Serial.print(",");
      Serial.print(gripperInput);
      Serial.print(">");

      int servonum = 0; // set the servo to the putter servo

      // move the putter back
      for (uint16_t pulselen = servo0_home; pulselen > SERVOMIN; pulselen--) {
        pwm.setPWM(servonum, 0, pulselen);
      }
      delay(500);

      // move the putter forward
      for (uint16_t pulselen = SERVOMIN; pulselen < SERVOMAX; pulselen++) {
        pwm.setPWM(servonum, 0, pulselen);
      }

      delay(500);

      pwm.setPWM(servonum, 0, servo0_home); // move the servo back home
      delay(500);
      digitalWrite(LED2, LOW);
    }
  }

  newData = false;
} // end while loop

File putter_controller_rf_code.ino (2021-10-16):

#include <SPI.h>
#include "printf.h"
#include "RF24.h"

#define rfStatusLED 4


RF24 radio(7, 8); // using pin 7 for the CE pin, and pin 8 for the CSN pin
uint8_t address[][6] = {"1Node", "2Node"};
bool radioNumber = 0; // 0 uses address[0] to transmit, 1 uses address[1] to transmit
float payload = 0.0;

struct Data_Package {
  int j1PotX;
  int j1PotY;
  int j2PotX;
  int j2PotY;
  //byte pot1;
  //byte pot2;
  //byte tSwitch1;
  //byte tSwitch2;
  byte button1;

};
Data_Package data; //Create a variable with the above structure
int button_state = 0;
int j1X = A0;
int j1Y = A1;
int j2X = A2;
int j2Y = A3;

const int button = 3;
const int deadBand = 200;

void setup() {

  Serial.begin(115200);
  while (!Serial) {
    // some boards need to wait to ensure access to serial over USB
  }

  // initialize the transceiver on the SPI bus
  if (!radio.begin()) {
    Serial.println(F("radio hardware is not responding!!"));
    while (1) {} // hold in infinite loop
  }

  Serial.print(F("radioNumber = "));
  Serial.println((int)radioNumber);

  radio.setPALevel(RF24_PA_LOW);  // RF24_PA_MAX is default.
  radio.setPayloadSize(sizeof(Data_Package)); // float datatype occupies 4 bytes
  radio.openWritingPipe(address[radioNumber]);     // always uses pipe 0
  radio.openReadingPipe(1, address[!radioNumber]); // using pipe 1
  radio.stopListening();  // put radio in TX mode

  data.j1PotX = 512;
  data.j1PotY = 512;
  data.j2PotX = 512;
  data.j2PotY = 512;
  //data.pot1 = 1;
  //data.pot2 = 1;
  //data.tSwitch1 = 1;
  //data.tSwitch2 = 1;
  data.button1 = 1;

  pinMode(3, INPUT_PULLUP);

} // setup

void loop() {
  // read the analog and digital inputs
  //byte j1PotX
  data.j1PotX = analogRead(A0);
  data.j1PotY = analogRead(A1);
  data.j2PotX = analogRead(A2);
  data.j2PotY = analogRead(A3);
  button_state = digitalRead(button);



  if (data.j1PotX > (512 - deadBand) && data.j1PotX < (512 + deadBand)) {
    data.j1PotX = 512;
  }
  if (data.j1PotY > 512 - deadBand && data.j1PotY < 512 + deadBand) {
    data.j1PotY = 512;
  }
  if (data.j2PotX > (512 - deadBand) && data.j2PotX < (512 + deadBand)) {
    data.j2PotX = 512;
  }
  if (data.j2PotY > 512 - deadBand && data.j2PotY < 512 + deadBand) {
    data.j2PotY = 512;
  }

  if (button_state == LOW)
  {
    Serial.println("button");
    data.button1 = 2;
  }
  else {
    data.button1 = 1;
  }


  Serial.print("j1PotX: ");
  Serial.print(data.j1PotX);
  Serial.print("j1PotY: ");
  Serial.print(data.j1PotY);
  Serial.print("j2PotX: ");
  Serial.print(data.j2PotX);
  Serial.print("j2PotY: ");
  Serial.print(data.j2PotY);
  Serial.print("button: ");
  Serial.println(data.button1);

  // This device is a TX node
  unsigned long start_timer = micros();                    // start the timer
  //bool report = radio.write(&payload, sizeof(Data_Package));      // transmit & save the report
  bool report = radio.write(&data, sizeof(Data_Package));      // transmit & save the report
  unsigned long end_timer = micros();                      // end the timer

  if (report) {
    digitalWrite(rfStatusLED, HIGH);
    Serial.print(F("Transmission successful! "));          // payload was delivered
    Serial.print(F("Time to transmit = "));
    Serial.print(end_timer - start_timer);                 // print the timer result
    Serial.print(F(" us. Sent: "));
    Serial.println(payload);                               // print payload sent
    payload += 0.01;                                       // increment float payload
  } else {
    Serial.println(F("Transmission failed or timed out")); // payload was not delivered
    digitalWrite(rfStatusLED, LOW);
  }

  // to make this example readable in the serial monitor
  delay(50);  // slow transmissions down by 1 second

} // loop

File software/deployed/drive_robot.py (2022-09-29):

#!/usr/bin/env python

import time
import serial
import tty, sys, termios, select
import Gamepad
#sys.path.insert(0, "/home/pi/")

# GLOBAL VARIABLES
# set frame rate - how many cycles/second to run the loop
FRAMERATE = 15
# how long does each frame take in seconds?
FRAME = 1.0/FRAMERATE
# initialize myTimer
topOfFrame = 0.0
endOfWork = 0.0
endOfFrame = 0.0
# how many cycles to test? counter*FRAME = runtime in seconds
counter = 2000
# fudge factor for our timing loop computations
TIME_CORRECTION = 0.0

timeError = 0.0
startup = True
CANCEL_MOVE_COUNT = 4 #number of loops unitl we send a 0 drive command
cancl_move_counter = 0

full_speed = 255 # what is the full speed of the robot, max is 255
current_speed_L = 0 # keep track of how fast the left motor is moving
current_speed_R = 0 # keep track of how fast the right motors is moving 
desired_speed = 0 # keep track of how fast the right motors is moving
current_speed = 0 # keep track of how fast the right motors is moving

prev_drive_messge_sent = False # track if we previously sent a drive message so we can send 0's if we want to stop

# controller setup
buttonHappy = 'CROSS'
buttonBeep = 'CIRCLE'
buttonExit = 'PS'
joystickLeftRight = 0 # right and left on D pad
joystickUpDown = 1 # up and down on D pad

dPadLeftRight = 6 # right and left on D pad
dPadUpDown = 7 # up and down on D pad

pollInterval = 0.2

# this class encapsulates our robot
class Robot():
    def __init__(self):
        # used to send commands to arduino and motors
        self.robotCommand = False  # is there a new command to send to robot?
        self.lastHeartBeat = 0.0  # time of the last heartbeat from Arduino

    def recHearBeat(self, hbTime):
        hbRecieved = time.time()
        self.latency = hbRecieved - hbTime
        self.lastHeartBeat = hbRecieved

    def vectorize(self):
        # this turns position, velocity, and accel into a vector
        self.vecX = [self.x, self.vx, self.ax]
        self.vecY = [self.y, self.vy, self.ay]
        self.ang = [self.yaw, self.vYaw, self.aYaw]


def readBuffer(buff):
    # the data we get is a series of lines separated by EOL symbols
    # we read to a EOL character (0x10) that is a line
    # process complete lines and save partial lines for later

    EOL = '>'
    if len(buff) == 0:
        return
    dataLine = ""
    lines = []
    for inChar in buff:
        if inChar != EOL:
            dataLine += inChar
        else:
            lines.append(dataLine)
            dataLine = ""
    for telemetryData in lines:
        processData(telemetryData)
    return dataLine


def processData(dataLine):
    # take information from the arduino and process telemetry into
    # status information
    # we recieve either heartbeat (HBB), telemetry list 1 (TL1), or error messages (ERR)

    dataType = dataLine[:3]
    payload = dataLine[3:]  # rest of the line is data
    if dataType == 'HBB':
        print(f"Heartbeat received: {payload}")
        
    if dataType == 'TL1':
        # process telemetry data
        pass
    if dataType == 'ERR':
        # process error data
        print("ARDUINO ERROR MESSSAGE ", payload)
        # log the error
        #rospy.loginfo(payload)
    return

# grab strokes from the keyboard and send them over
def isData():
    return select.select([sys.stdin], [], [], 0) == ([sys.stdin], [], [])

def leftRightAxisMoved(position):
    global leftRight
    leftRight = position   # Inverted
    print(leftRight)

def upDownAxisMoved(position):
    global upDown
    upDown = position # Non-inverted
    print(upDown)

def getSpeed(postion):
    global current_speed_R
    global current_speed_L

# initialize the joysticks
if not Gamepad.available():
    print('Please connect your gamepad...')
    while not Gamepad.available():
        time.sleep(1.0)
gamepad = Gamepad.Gamepad()
print('Gamepad connected')
gamepad.startBackgroundUpdates()


# main program start here
# *********************************************************************
robot = Robot()  # define our robot instance
serialPort = "/dev/ttyACM0"
# open the serial port to arduino
ser = serial.Serial(serialPort,115200,timeout=0)
# serial port with setting 38,400 baud, 8 bits, No parity, 1 stop bit=
ser.reset_input_buffer()

# Set some initial state
leftRight = 0.0
upDown = 0.0
gamepad.addAxisMovedHandler(joystickLeftRight, leftRightAxisMoved)
gamepad.addAxisMovedHandler(joystickUpDown, upDownAxisMoved)

frameKnt = 0  # counter used to time processes
newDriveMessage = False
newPuttMessage = False

try:
    while True:

        if not Gamepad.available():
            print('Please connect your gamepad...')
            while not Gamepad.available():
                time.sleep(1.0)
            gamepad = Gamepad.Gamepad()
            print('Gamepad connected')
            gamepad.startBackgroundUpdates()

        # main loop
        topOfFrame = time.time()

        # read data from serial port
        if ser.in_waiting > 0:
            serData = ser.readline().decode('utf-8').rstrip()
            if len(serData) > 0:
                print(f"serial data: {serData}")
        # process the data from the arduino
        # read and parse the lines to avoid any blocking
            holdBuffer = readBuffer(serData)

        com = ','
        EOL = '>'

        # check if the controller has been used
        if gamepad.beenPressed(0): # A
            print("A Pressed")
            robMessage = "DRV"+com+str(0)+com+str(0)+EOL
            newDriveMessage = True
        if gamepad.beenPressed(1): # B
            print("B Pressed")
            newPuttMessage = True
        if gamepad.beenReleased(0): # A
            print("A Released")
        if gamepad.beenReleased(1): # B
            print("B Released")

        # set speeds, range (0-255)
        if upDown > .25 or upDown < -.25:
            desired_speed = int(full_speed * abs(upDown))
        elif leftRight < -.25 or leftRight > .25:
            desired_speed = int(full_speed * abs(leftRight))
        else:
            desired_speed = 0

        #print("Desired speed: ", desired_speed)

        if desired_speed > full_speed:
            desired_speed = full_speed
        if desired_speed > 0 and desired_speed < 60:
            desired_speed = 60

        current_speed = desired_speed
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
